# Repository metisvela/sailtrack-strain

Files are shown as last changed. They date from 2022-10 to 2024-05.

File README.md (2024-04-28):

<p align="center">
  
</p>

<p align="center">
  
  
</p>

# SailTrack Strain

SailTrack Strain is a component of the SailTrack system, it manages load cells mounted on the boat maneuvers, providing load and stress information about them. To learn more about the SailTrack project, please visit the [project repository](https://github.com/metisvela/sailtrack).

The SailTrack Strain module is based on a battery powered LilyGo TTGO T7, consisting of an [ESP32](https://www.espressif.com/en/products/socs/esp32) microcontroller, connected to an Operational Amplifier breakout board connected to a load cell, mounted "in parallel" to the boat shroud. For a more detailed hardware description of the module, please refer to the [Bill Of Materials](hardware/BOM.csv). The 3D-printable enclosure con be found [here](hardware/STL).

The module performs the following tasks:

* It gets the raw load cell measurments, it amplifies and converts them to readable values and it sends them to the SailTrack Network.

<p align="center">
  <br/>
  
</p>

module-image

## Installation

Follow the instructions below to get the SailTrack Strain firmware correctly installed. If you encounter any problem, please [open an issue](https://github.com/metisvela/sailtrack-strain/issues/new).

1. [Install PlatformIO Core](https://docs.platformio.org/en/latest/core/installation/index.html).
2. Clone the SailTrack Strain repository:
   ```
   git clone https://github.com/metisvela/sailtrack-strain.git 
   ``` 
3. Cd into the directory:
   ```
   cd sailtrack-strain
   ```
4. **(macOS ONLY)** Uncomment the commented lines after "Patch for macOS" in the `platformio.ini` file.
5. Connect the module with an USB cable.
6. Finally, flash the firmware:
   ```
   pio run
   ```

## Usage

Once the firmware is uploaded the module can work with the SailTrack system. When SailTrack Strain is turned on, a LED start to blink to notify the user about the connection status with SailTrack Core. Then, if the connection is successful, the LED stays on, otherwise the module will put itself to sleep, and it will try to connect later. Once the module is connected it will automatically start sending measurements.

## Contributing

Contributors are welcome. If you are a student of the University of Padova, please apply for the Metis Sailing Team in the [website](http://metisvela.dii.unipd.it), specifying in the appliaction form that you are interested in contributing to the SailTrack Project. If you are not a student of the University of Padova, feel free to open Pull Requests and Issues to contribute to the project.

## License

Copyright © 2023, [Metis Sailing Team](https://github.com/metisvela). SailTrack Strain is available under the [GPL-3.0 license](https://www.gnu.org/licenses/gpl-3.0.en.html). See the LICENSE file for more info.

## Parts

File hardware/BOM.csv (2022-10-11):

Part Name | Total Quantity Required | Note
LilyGo TTGO T7 v1.3 ESP32-WROVER-B + BMS | 1
HX711 Load Cell Amplifier Module | 1
Load Cell | 1 | DIY (BF-350 Strain Gauges) or Buy
103040 LiPo Battery 1S 1200mAh | 1

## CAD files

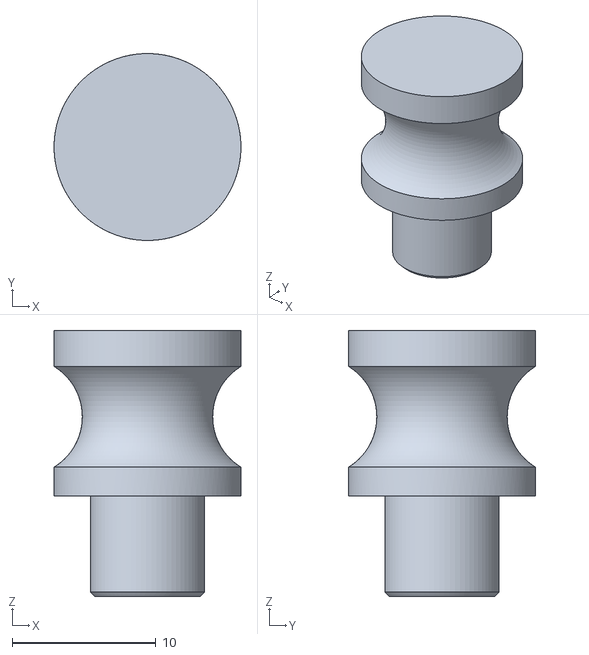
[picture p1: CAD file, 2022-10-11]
hardware/STL/Fairlead.stl
13.0 x 13.0 x 18.5

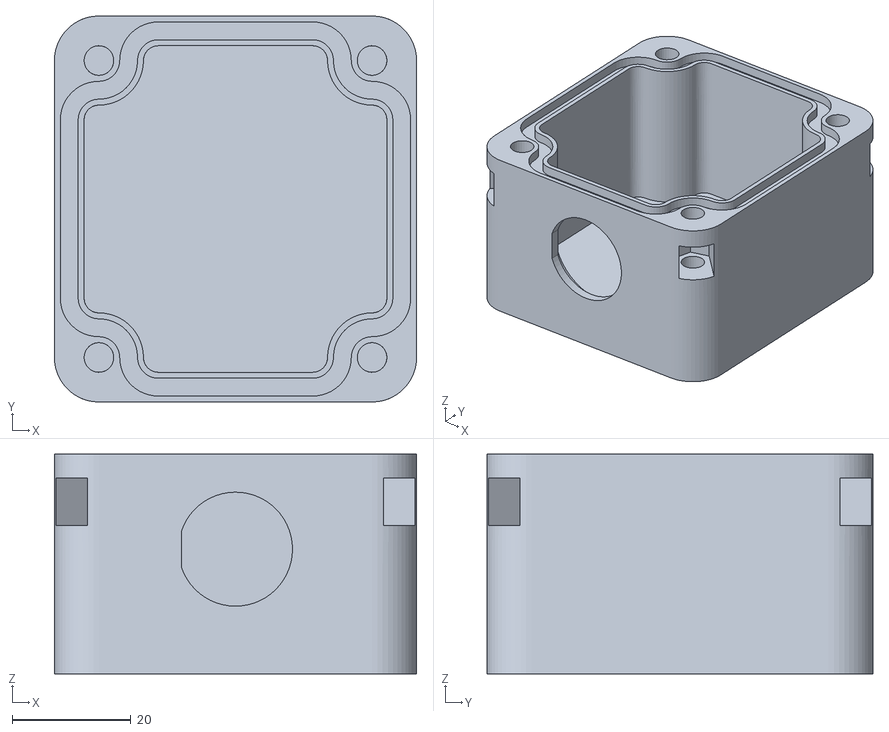
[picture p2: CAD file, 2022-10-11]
hardware/STL/Case Bottom.stl
61.0 x 65.0 x 37.0

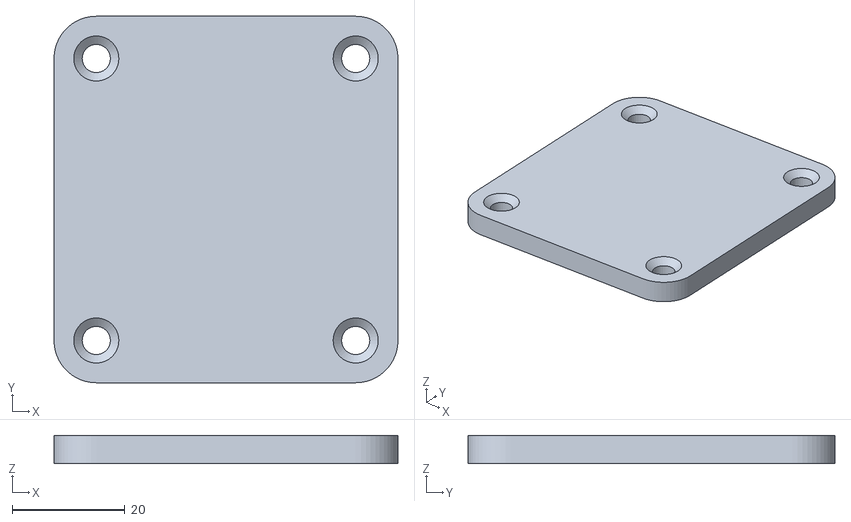
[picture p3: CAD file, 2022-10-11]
hardware/STL/Case Top.stl
61.0 x 65.0 x 5.00

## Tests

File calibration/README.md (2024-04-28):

# Strain Calibration

This README provides instructions for calibrating the Strain sensor using the shrouds of a rigged boat using a Python script.

## Prerequisites
* Python installed on your system.
* Both strain_left sand strain_right sensors.
* Access to the shrouds of the rigged boat.

## Calibration Procedure
* Set the right python interpreter with the right dependencies.
* Before proceeding further, it is crucial to allow the sensor to rest without applying any tension. This ensures accurate baseline measurements.
* Run the Python Script: Execute the Python script provided in the repository.
* Follow On-screen Instructions: The script will guide you through the calibration process. Ensure you carefully follow each step as instructed.
* Attach the sensors on both shrouds: Once prompted by the script, attach the tension sensor securely to the shroud of the rigged boat.

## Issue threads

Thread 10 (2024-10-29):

3D-printable enclosure lid/top + screws

wasauce, 2024-10-29:
Hello!

I greatly appreciate your project and you posting the stl files for the enclosure.

In your photos you have a clear lid. What material did you use to print that clear lid? Where did you go to do that?

Example: https://github.com/metisvela/sailtrack-core/blob/main/hardware/Module%20Image.jpg

Also I see a set of screws used to keep the lid on, what size are they?

Thank you!

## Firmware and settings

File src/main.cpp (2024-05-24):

#include <Arduino.h>
#include <SailtrackModule.h>
#include <HX711.h>
#include <EEPROM.h>

// -------------------------- Configuration -------------------------- //

#define MQTT_PUBLISH_FREQ_HZ		5

#define BATTERY_ADC_PIN 		    35
#define BATTERY_ADC_RESOLUTION 		4095
#define BATTERY_ADC_REF_VOLTAGE 	1.1
#define BATTERY_ESP32_REF_VOLTAGE	3.3
#define BATTERY_NUM_READINGS 	  	32
#define BATTERY_READING_DELAY_MS	20

#define HX711_DOUT_PIN				16
#define HX711_SCK_PIN				17
#define HX711_NUM_READING			1

#define LOOP_TASK_INTERVAL_MS		1000 / MQTT_PUBLISH_FREQ_HZ

#define EEPROM_ALLOC_SIZE_BYTES		512
#define EEPROM_CAL_SIZE_BYTES		2+sizeof(long)+sizeof(float)+2
#define EEPROM_CAL_ADDR				42
#define EEPROM_CAL_ID_0				0x30
#define EEPROM_CAL_ID_1				0x55

#define CAL_TARE_DELAY_S			10
#define CAL_NUM_READINGS			10
#define	CAL_SCALE_DELAY_S			10
#define CAL_TARE_LED_DELAY_MS		700
#define CAL_SCALE_LED_DELAY_MS		200
#define CAL_NUM_TRIES				5
#define CAL_TRIES_DELAY_MS			500
#define CAL_ERROR_LED_DELAY_MS		150		
#define CAL_ERROR_BLINKING_TIMES 	3
// ------------------------------------------------------------------- //

SailtrackModule stm;
HX711 hx;
/*
	offset->tare
	scale->divider
*/
bool calibration;
int calibrationTries=CAL_NUM_TRIES;
int calibrationScaleDelay;
float calibrationLoad;
/**
 * @brief This class contains functions that will be called asynchronously by the SailTrack Module library.
 * 
 */
class ModuleCallbacks: public SailtrackModuleCallbacks {
	/**
	 * @brief This function appends battery status to the other hardware informations provided by the Json 
	 * status.
	 * @details This function is called asynchronously by the SailTrack Module library when it necessary
	 * to know battery information.
	 * Battery information is calculated over BATTERY_NUM_READINGS readings to have a more robust value.
	 * 
	 * @param status is the Json object the stores hardware informations.
	 */
	void onStatusPublish(JsonObject status) {
		JsonObject battery = status.createNestedObject("battery");
		float avg = 0;
		for (int i = 0; i < BATTERY_NUM_READINGS; i++) {
			avg += analogRead(BATTERY_ADC_PIN) / BATTERY_NUM_READINGS;
			delay(BATTERY_READING_DELAY_MS);
		}
		battery["voltage"] = 2 * avg / BATTERY_ADC_RESOLUTION * BATTERY_ESP32_REF_VOLTAGE * BATTERY_ADC_REF_VOLTAGE;
	}
	/**
	 * @brief This function initiate the calibration procedure by setting load and time to attach 
	 * the load cell to the shroud.
	 * 
	 * @details When the MQTT message has been sent, it calls asynchronously this function that starts the
	 * calibration procedure.
	 * By using MQTT protocol MQTT message is simply a Json file.
	 * The sender of the message can provide two values:
	 * load of the shroud->compulsory
	 * time to attach the load cell to the shroud->not compulsory
	 * If time is not provided, it will be used default value.
	 * 
	 * @param topic is the "scope" where the message has been published.
	 * 
	 * @param message is what has been sent via MQTT protocol
	 */
	void onMqttMessage(const char * topic, JsonObjectConst message) {
		calibrationLoad=message["calibrationLoad"];
		//calibrationScaleDelay is optional. If it has not been provided, it will be set to the default value CAL_SCALE_DELAY_S
		calibrationScaleDelay=message["calibrationScaleDelay"]?message["calibrationScaleDelay"]:CAL_SCALE_DELAY_S;
		calibration=true;
	}

};
/**
 * @brief This function does the CYCLIC REDUNDANCY CHECK for the memory area that stores the offset and divider.
 * 
 * @details This function operates the incremental CYCLIC REDUNDANCY CHECK by using xor operations with 0xA001 polynomial.
 * The remainder of the division is the CRC.
 * 
 * @param crc the actual remainder
 * 
 * @param a the payload over to operate the CRC.
 * 
 * @return uint16_t is the result of the CRC operation
 */
uint16_t crc16Update(uint16_t crc, uint8_t a) {
    int i;
	//logic xor
    crc ^= a;
    for (i = 0; i < 8; i++) {
        if (crc & 1) crc = (crc >> 1) ^ 0xA001;
        else crc = (crc >> 1);
    }
    return crc;
}
/**
 * @brief It loads offset and divider value into amplifier system.
 * 
 * @details It loads offset and divider value into amplifier system.
 * If the crc reveals some problems, the load calibration operation will not be performed.
 * Before getting offset and divider values from memory, the algorithm checks whether the checksum result
 * from offset and divider just read from memory and the checksum stored in memory is zero (calculated previously
 * while saving values into memory).
 * If the result is zero, it means that the data hadn't been corrupted.
 * 
 * @return true if the load of the calibration works properly.
 * 
 * @return false otherwise.
 */
bool loadCalibration() {
	uint8_t buf[EEPROM_CAL_SIZE_BYTES];
	uint16_t crc = 0xFFFF;
	for (uint16_t a = 0; a < EEPROM_CAL_SIZE_BYTES; a++) {
		buf[a] = EEPROM.read(a + EEPROM_CAL_ADDR);
		crc = crc16Update(crc, buf[a]);
	}
	//if the are data corrupted crc is not zero.
	if (crc != 0 || buf[0] != EEPROM_CAL_ID_0 || buf[1] != EEPROM_CAL_ID_1) 
		return false;	


	long offset;
	//divider=scale
	float scale;
	memcpy(&offset, buf + 2, sizeof(offset));
	memcpy(&scale,buf+2+sizeof(offset),sizeof(scale));
	hx.set_offset(offset);
	hx.set_scale(scale);

	return true;
}

/**
 * @brief This routine carries out the saving operation of the calibration.
 * 
 * @details this function stores offset and divider values into the EEPROM memory for future uses.
 * It uses crc to check wheter the memory had been written before.
 * After adding offset and divider values into the memory, the algoritm appends the checksum of those values
 * to check while getting values from memory, if they had been modified or not.
 * 
 * @return true if the saving calibration operation works properly
 * 
 * @return false otherwise
 */
bool saveCalibration() {

	uint8_t buf[EEPROM_CAL_SIZE_BYTES];
	//set to zero EEPROM_CAL_SIZE_BYTES pointed by buf
	memset(buf, 0, EEPROM_CAL_SIZE_BYTES);
	buf[0] = EEPROM_CAL_ID_0;
	buf[1] = EEPROM_CAL_ID_1;

	long offset=hx.get_offset();
	float scale=hx.get_scale();
	memcpy(buf+2,&offset,sizeof(offset));
	memcpy(buf+2+sizeof(offset),&scale,sizeof(scale));

	uint16_t crc = 0xFFFF;
	for (uint16_t i = 0; i < EEPROM_CAL_SIZE_BYTES - 2; i++) 
		crc = crc16Update(crc, buf[i]);
	buf[EEPROM_CAL_SIZE_BYTES - 2] = crc & 0xFF;
	buf[EEPROM_CAL_SIZE_BYTES - 1] = crc >> 8;

	for (uint16_t a = 0; a < EEPROM_CAL_SIZE_BYTES; a++) 
		EEPROM.write(a + EEPROM_CAL_ADDR, buf[a]);

	EEPROM.commit();
	
	return true;
}

/**
 * @brief This function set the tare and scale value based on the given load,
 * passed by the parameter calLoad.
 * 
 * @details The function starts by checking whether the passed parameter is zero or not.
 * The first blinking carried out onto the onboard led, is necessary to tell the user
 * that the setting tare block is ongoing.
 * The second blinking is used for the setting scale procedure.
 * Tare blinking and scale blinking are performed at different speed.
 * Lastly, the two values are stored into the EEPROM memory of the ESP32 microcontroller.
 * 
 * @param calLoad is the value used for calibrating the load cell.
 * 
 * @param calScaleDelay refers to the time necessary to attach the load cell
 * to the shroud.
 * 
 * @return true if the calibration process terminates correctly.
 * 
 * @return false if the are some problems with calibration procedure.
 */
bool calibrate(float calLoad, int calScaleDelay){
	//if zero return false
	if(!calLoad) return false;
	//set tare
	for(int i=0;i<(1000*CAL_TARE_DELAY_S)/(2*CAL_TARE_LED_DELAY_MS);i++){		
		digitalWrite(STM_NOTIFICATION_LED_PIN, LOW);
		delay(CAL_TARE_LED_DELAY_MS);
		digitalWrite(STM_NOTIFICATION_LED_PIN, HIGH);
		delay(CAL_TARE_LED_DELAY_MS);
	}
	hx.tare(CAL_NUM_READINGS);
	//set scale	
	for(int i=0;i<(1000*calScaleDelay)/(2*CAL_SCALE_LED_DELAY_MS);i++){		
		digitalWrite(STM_NOTIFICATION_LED_PIN, LOW);
		delay(CAL_SCALE_LED_DELAY_MS);
		digitalWrite(STM_NOTIFICATION_LED_PIN, HIGH);
		delay(CAL_SCALE_LED_DELAY_MS);
	}
	double reading=hx.get_value(CAL_NUM_READINGS);
	//set new scale
	hx.set_scale(reading/calLoad);
	return saveCalibration();
}
/**
 * @brief The readData is responsible for publishing the raw and load data of
 * the load cell.
 * 
 * @details This function creates a new Json object, useful to store the raw reading from
 * the load cell and the actual load calculated by the load cell.
 * The raw reading is the average of HX711_NUM_READING values.
 * At the end the Json object is published in the sensor/strain0 topic. 
 */
void readData(){	
	TickType_t lastWakeTime = xTaskGetTickCount();
	StaticJsonDocument<STM_JSON_DOCUMENT_MEDIUM_SIZE> doc;	
	doc["raw"]=hx.read_average(HX711_NUM_READING);
	doc["load"]=hx.get_units(HX711_NUM_READING);
	stm.publish("sensor/strain0", doc.as<JsonObjectConst>());	
	vTaskDelayUntil(&lastWakeTime, pdMS_TO_TICKS(LOOP_TASK_INTERVAL_MS));
}
/**
 * @brief Setup function is used to initiliaze the system.
 * 
 * @details The following procedures are executed:
 * The system amplifier is initiated with the hx.begin() function.
 * EEPROM size used to store the data is set with EEPROM.begin().
 * The system loads the previous calibration stored in the EEPROM memory.
 * It subscribes to the sensor/strain0/calibration topic,
 *  to be able to receive MQTT messages from that topic.
 */
void setup() {
	stm.begin("strain", IPAddress(192, 168, 42, 105), new ModuleCallbacks());
	hx.begin(HX711_DOUT_PIN, HX711_SCK_PIN);
	EEPROM.begin(EEPROM_ALLOC_SIZE_BYTES);
	loadCalibration();
	stm.subscribe("sensor/strain0/calibration");
}
/**
 * @brief Loop performs the calibration process or the reading data process.
 * 
 * @details It can either perform the calibration function or the reading data procedure.
 * If the calibrate operation return false for some error, it will be performed a blinking to
 * signal it.
 * Once the calibration ends correctly, the reading data operation will start.
 */
void loop() {
	
	if(calibration){
		if(calibrate(calibrationLoad,calibrationScaleDelay)){
			calibration=false;
			calibrationTries=CAL_NUM_TRIES;
		}
		else
			{
				for(int i=0;i<CAL_ERROR_BLINKING_TIMES;i++){
					digitalWrite(STM_NOTIFICATION_LED_PIN, LOW);
					delay(CAL_ERROR_LED_DELAY_MS);
					digitalWrite(STM_NOTIFICATION_LED_PIN, HIGH);
					delay(CAL_ERROR_LED_DELAY_MS);
				}
				if(!calibrationTries--){
					calibration=false;
					calibrationTries=CAL_NUM_TRIES;
				}									
				delay(CAL_TRIES_DELAY_MS);
			}
	}
	else
		readData();	
	
}

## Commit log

2021-07-06 Added submodule lib/sailtrack-sensor
2022-02-17 Add hardware fiels
    [BOM.csv]
2022-07-08 Add calibration test
2022-07-17 create the calibration function
2022-07-22 Testing calibration function
2022-07-28 Update hardware files
    [Case Bottom.stl, Case Top.stl]
2022-10-11 Add Fairlead STL file
    [Fairlead.stl]
2024-04-28 Add calibration script + readme
2024-05-24 fix pinout for esp32-s3
    [main.cpp]
